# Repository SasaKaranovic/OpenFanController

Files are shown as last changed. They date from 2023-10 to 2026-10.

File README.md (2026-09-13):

# DIY OpenFAN Controller

## What is this project about?

DIY OpenFAN Controller (http://www.youtube.com/watch?v=C8tcsyASQRM "DIY OpenFAN Controller")

Above video shows the finished 10 channel PC fan controller, how it works and motivation behind some of the design decisions.

Some of the main features of the OpenFAN controller are:

- Individually control up to 10 fans
- USB communication with the host PC
- Has a built-in USB bootloader for smooth firmware upgrade experience
- GUI to control and monitor fans. Accessible locally/remotely through web browser
- Control fans by setting PWM percentage or target RPM
- Supports virtually unlimited number of custom fan profiles that you can create and apply through GUI/API
- Built in API interface for integration, (remote) monitoring or (remote) control.
- Built using simple off-the-shelf components to make it hacker/diy friendly
- Designed to be platform/OS agnostic and works on Windows, Linux and Mac
- GUI/API can be deployed as Docker application
- <a href="https://getfancontrol.com/" target="_blank">Fan Control</a> integration through <a href="https://github.com/SasaKaranovic/FanControl.OpenFan" target="_blank">FanControl.OpenFAN<a/> plugin (Windows)
- <a href="https://unraid.net/community/apps?q=OpenFanController#r" target="_blank">Unraid</a> docker integration through <a href="https://unraid.net/community/apps?q=OpenFanController#r" target="_blank">OpenFanController<a/> application (Unraid)
- <a href="https://github.com/SasaKaranovic/OpenFanController/pkgs/container/openfancontroller" target="_blank">Docker</a> image available (Docker)
<br/><br/>

## Can I buy OpenFAN controller

Yes you can. It's available on the [web shop](https://shop.sasakaranovic.com/products/openfan-pc-fan-controller).
<br/><br/>

## Can I build my own?

Yes you can. The above video explains the idea and how hardware and firmware works. It's recommended that you watch that first.

Hardware, Firmware and Software build instructions and source files are available in this repository.
<br/><br/>

## Is there documentation?

Documentation for OpenFAN Controller (and other projects) can be found at the official [docs page](https://docs.sasakaranovic.com/openfan/).
<br/><br/>

## What platforms are supported?

OpenFAN is designed to be platform agnostic. This means you can use it on Windows, Linux and Mac.

You can find more information on how to run OpenFAN software in the [software read me](Software)
<br><br>

Blog page: https://sasakaranovic.com/projects/openfan-controller/

YouTube video: http://www.youtube.com/watch?v=C8tcsyASQRM

<br/><br/>

#### Sasa Karanovic

<a href="https://sasakaranovic.com/" target="_blank" title="Sasa Karanovic Home Page"> Home Page</a> &nbsp;&middot;&nbsp;
<a href="https://youtube.com/c/sasakaranovic" target="_blank" title="Sasa Karanovic on YouTube"> YouTube</a> &nbsp;&middot;&nbsp;
<a href="https://github.com/sasakaranovic" target="_blank" title="Sasa Karanovic on GitHub"> GitHub</a> &nbsp;&middot;&nbsp;
<a href="https://twitter.com/_sasakaranovic_" target="_blank" title="Sasa Karanovic on Twitter"> Twitter</a> &nbsp;&middot;&nbsp;
<a href="https://instagram.com/_sasakaranovic_" target="_blank" title="Sasa Karanovic on Instagram"> Instagram</a> &nbsp;&middot;&nbsp;
<a href="https://github.com/sponsors/SasaKaranovic" target="_blank" title="Sponsor on GitHub"> Sponsor on GitHub</a>

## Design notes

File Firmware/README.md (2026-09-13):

# OpenFAN Controller - Firmware

## How to install latest firmware onto the board?

OpenFAN Controller supports loading new firmware over USB.

Latest firmware is compiled through GitHub action and published under [releases](https://github.com/SasaKaranovic/OpenFanController/releases). Download the latest firmware version to your PC.

To load the latest firmware onto your board, follow the below steps:

1. Disconnect all fans and power from the board
2. Hold the BOOT button
3. Connect USB-C cable to OpenFAN
4. You should see a new USB drive on your PC
5. Drag and drop (or copy-paste) the OpenFAN firmware
6. Within few seconds, the drive will disappear and you should see the white LED on the OpenFAN blinking
7. The board should be flashed and ready to go now
8. As a precaution and just to be 100% sure, you should power cycle the OpenFAN before using it.

## How to build firmware?

OpenFAN controller uses Pico2040 as the main microcontroller.

In order to build the firmware, you will need to install and setup Pico-SDK first. After that you can run `build.sh` script or manually run through the following steps

- `cmake -B {path-to-pico-sdk-directory} -S {path-to-OpenFAN-firmware-src-directory}`
- `cmake -C build`

If everything runs successfully, you should see a `build` folder and inside there should be a `.uf2` file that you can use for firmware upgrade.

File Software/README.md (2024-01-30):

# OpenFAN Controller - Software

## How to run the software?

There are many ways to run the OpenFAN software.

### Running from source [Win/Linux/Mac]

On any OS, if you have Python 3.9 (or higher) and PIP installed, you can run from source code.

1. Clone this repository and navigate to `Software/Python` folder.
2. Install Python dependencies by running `pip install -r requirements.txt`
3. Run the main application with `python webserver.py`
4. Open `http://localhost:3000` to access the Web GUI
<br><br>

### Running with Docker [Windows/Linux/Mac]

You can run OpenFAN in a Docker container.

Since with OpenFAN you can control fans remotely (via API and/or Web GUI), this can be very helpful for remotely managing fans on your servers or media stations.

To create a Docker container, log into your machine and run following commands

1. docker build github.com/sasakaranovic/openfancontroller -t sasakaranovic/openfan
2. docker run --name OpenFAN -p 3000:3000 --device=/dev/ttyACM0 -e OPENFANCOMPORT=/dev/ttyACM0 sasakaranovic/openfan:latest
3. Make sure you can access the server running this container and configure your firewall to allow port `3000` (if necessary)
4. Open `http://server-ip:3000` to access the Web GUI
<br><br>

### Using Fan Control [Windows]

You can use your OpenFAN directly from [Fan Control](https://getfancontrol.com/).

Fan Control is a highly focused fan controlling software for Windows.

To use OpenFAN with Fan Control, you can download the `FanControl.OpenFAN` plugin.

1. Install [Fan Control](https://getfancontrol.com/)
2. Download [FanControl.OpenFAN](https://github.com/SasaKaranovic/FanControl.OpenFan) plugin
3. Copy `FanControl.OpenFan.dll` to Fan Control's `Plugins` folder. (You might need to "unlock" the dll in its properties.)
4. Restart Fan Control
5. Fan Control will display all OpenFAN fan controls and RPM sensors
<br><br>

## How to debug/develop the software?

OpenFAN Controller is written in Python. In order to run the code, you will need to install Python 3.9 or higher.

After that, you will need to install the PIP Python package manager.

### Install dependencies

In order to install project dependencies you can open a terminal and navigate to the OpenFAN `Software/Python` directory.

Then type `pip install -r requirements.txt`

This will install all the necessary dependencies.

### How to run the server application

In your terminal, navigate to the `Software/Python` directory of OpenFAN and type `python webserver.py`

This will start the OpenFAN server. After this you can start using the gui through web browser by openning `https://localhost:3000` or use the API as described in the documentation.

### Running without Python or Docker?

There are multiple ways of converting a python code to an executable (ie. `py2exe`, `pyinstaller` etc).

There are many tutorials on how to do this depending on your operating system.

In the future, I will try to use GitHub Actions to generate binaries and installers that you can use to easily install and run OpenFAN software.

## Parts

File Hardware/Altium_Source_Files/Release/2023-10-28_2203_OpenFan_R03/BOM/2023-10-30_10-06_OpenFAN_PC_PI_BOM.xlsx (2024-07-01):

Designator | Manufacturer | Manufacturer Part Number | Quantity
C1 | KEMET | A768KE227M1DLAE029 | 1
C2, C4, C6, C10, C11, C12, C13, C14, C15, C16, C17, C18, C19, C21, C22, C24 | Samsung Electro-Mechanics | CL10B104KB8NNNC | 16
C5, C9, C20 | Samsung Electro-Mechanics | CL10A225KA8NNNC | 3
C7, C8 | Samsung Electro-Mechanics | CL10C070CB8NNNC | 2
C23_FCN1, C23_FCN2, C23_FCN3, C23_FCN4, C23_FCN5, C23_FCN6, C23_FCN7, C23_FCN8, C23_FCN9, C23_FCN10 | Samsung Electro-Mechanics | CL10A105KA8NNNC | 10
C25 | Samsung Electro-Mechanics | CL21A106KAYNNNE | 1
C26, C27 | Samsung Electro-Mechanics | CL21A226MAYNNNE | 2
D1 | ams-OSRAM USA INC. | LW Q38G-Q2OO-3K5L-1 | 1
F1, F2, F3 | Bel Fuse Inc. | 0ZCM0020FF2G | 3
L1 | Murata Electronics | LQM31PN4R7M00L | 1
P1 | Bestcreate Technology Limited | S150-M1A5T-003, S150-M2A5T-003, S150-M3A5T-003, | 1
P2 | Amphenol ICC (FCI) | 10118192-0001LF | 1
P4_FCN1, P4_FCN2, P4_FCN3, P4_FCN4, P4_FCN5, P4_FCN6, P4_FCN7, P4_FCN8, P4_FCN9, P4_FCN10 | Molex | 0470531000 | 10
R1, R2 | YAGEO | AC0603FR-0727RL | 2
R3 | YAGEO | RC0603FR-074K7L | 1
R4, R5, R11 | YAGEO | RC0603FR-0710KL | 3
R6, R15 | YAGEO | RC0603FR-071KL | 2
R7, R8, R10, R14, R16, R17 | YAGEO | RC0603FR-102K2L | 6
R9 | YAGEO | RC0603FR-10470RL | 1
R12 | YAGEO | RC0603FR-1015KL | 1
R13_FCN1, R13_FCN2, R13_FCN3, R13_FCN4, R13_FCN5, R13_FCN6, R13_FCN7, R13_FCN8, R13_FCN9, R13_FCN10 | YAGEO | RC0603FR-07100KL | 10
SW1, SW2 | E-Switch | TL1015AF160QG | 2
U1 | Winbond Electronics | W25Q32JVZPIQ | 1
U2 | Raspberry Pi | SC0914(13) | 1
U3, U4 | Microchip Technology | EMC2305-1-AP-TR | 2
U5 | Diodes Incorporated | AP63203WU-7 | 1
X1 | Abracon LLC | ABMM2-12.000MHZ-E2-T | 1

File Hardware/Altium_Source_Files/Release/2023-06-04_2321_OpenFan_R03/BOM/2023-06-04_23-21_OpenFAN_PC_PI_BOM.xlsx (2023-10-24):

Designator | Distributor | Distributor Part Number | Manufacturer | Manufacturer Part Number | Quantity
C1 | DigiKey | 399-A768KE227M1DLAE029TR-ND | KEMET | A768KE227M1DLAE029 | 1
C2, C4, C5, C6, C7, C8, C9, C10, C11, C12, C13, C14, C15, C16, C17, C18, C19, C20, C21, C22, C23_FCN1, C23_FCN2, C23_FCN3, C23_FCN4, C23_FCN5, C23_FCN6, C23_FCN7, C23_FCN8, C23_FCN9, C23_FCN10, C24, C25, C26, C27, D1, F1, F2, F3, L1, P1, P2, R1, R2, R3, R4, R5, R6, R7, R8, R9, R10, R11, R12, R13_FCN1, R13_FCN2, R13_FCN3, R13_FCN4, R13_FCN5, R13_FCN6, R13_FCN7, R13_FCN8, R13_FCN9, R13_FCN10, R14, R15, R16, R17, SW1, SW2 | [NoValue], DigiKey |  |  |  | 69
P3, P5 | DigiKey | A135088-ND | TE Connectivity AMP Connectors | 1546215-4 | 2
P4_FCN1, P4_FCN2, P4_FCN3, P4_FCN4, P4_FCN5, P4_FCN6, P4_FCN7, P4_FCN8, P4_FCN9, P4_FCN10 | DigiKey | WM4330-ND | Molex | 0470531000 | 10
U1 | DigiKey | W25Q32JVZPIQ-ND | Winbond Electronics | W25Q32JVZPIQ | 1
U2 | DigiKey | 2648-SC0914(13)CT-ND | Raspberry Pi | SC0914(13) | 1
U3, U4 | DigiKey | EMC2305-1-AP-CT-ND | Microchip Technology | EMC2305-1-AP-TR | 2
U5 | DigiKey | AP63203WU-7DICT-ND | Diodes Incorporated | AP63203WU-7 | 1
X1 | DigiKey | 535-9631-1-ND | Abracon LLC | ABMM2-12.000MHZ-E2-T | 1

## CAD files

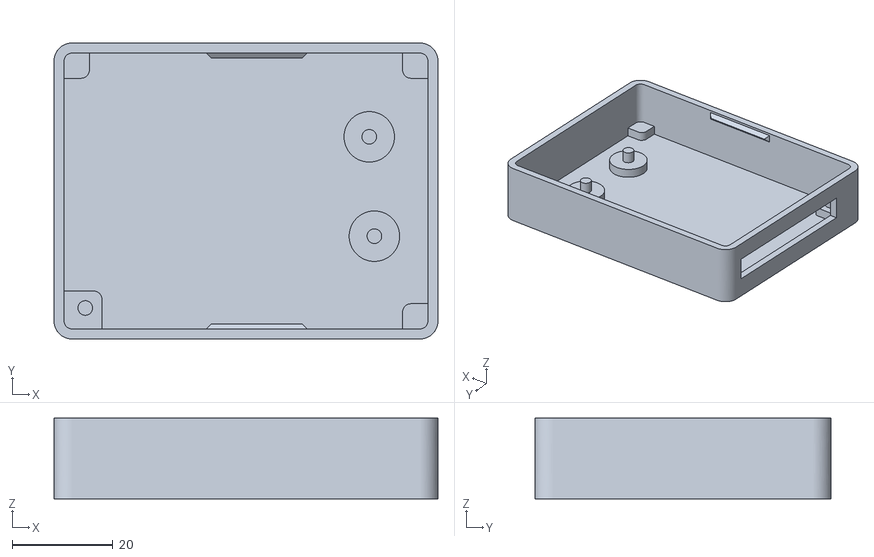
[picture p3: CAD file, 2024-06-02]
Enclosure/Rev1/Enclosure_OpenFAN_Bottom.stl
76.1 x 58.7 x 16.0

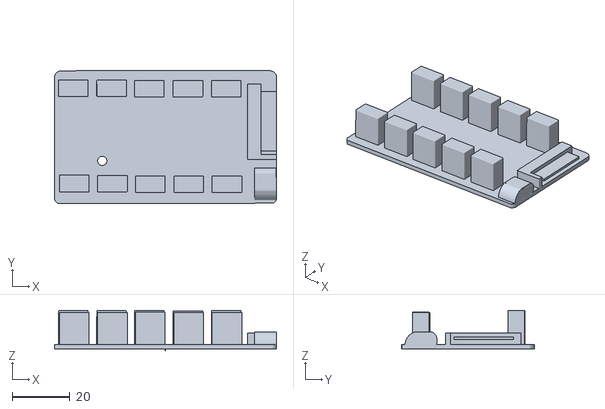
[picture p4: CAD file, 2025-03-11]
Enclosure/Rev2_by_Joe_Dutson/New_V7_PCB.stl
77.0 x 46.0 x 13.9

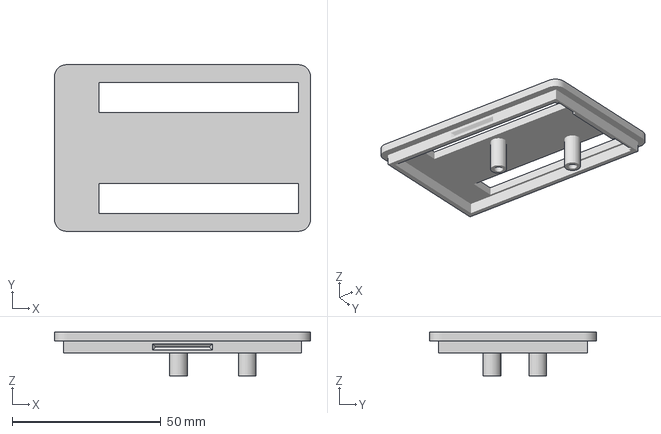
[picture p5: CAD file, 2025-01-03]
Enclosure/Rev2_by_Sam_Chan/Top-PCB-Enclosure_by_Sam_Chan.3mf
86.0 x 56.0 x 14.7 mm

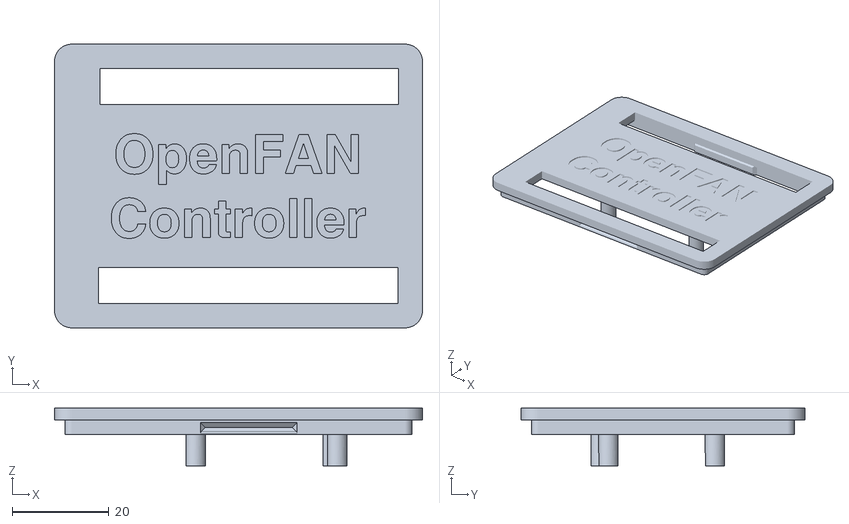
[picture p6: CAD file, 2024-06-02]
Enclosure/Rev1/Enclosure_OpenFAN_Top.stl
76.1 x 58.7 x 11.9

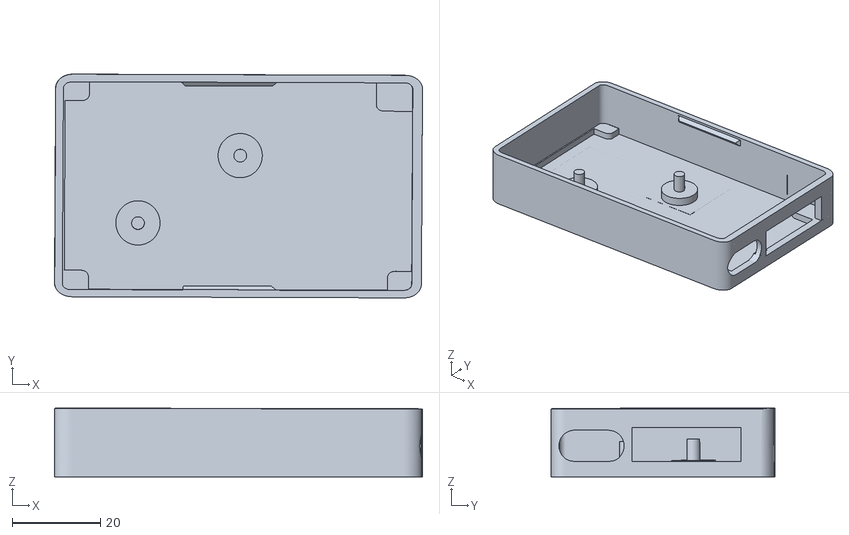
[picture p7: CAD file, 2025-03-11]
Enclosure/Rev2_by_Joe_Dutson/New_V7_Bottom.stl
83.2 x 50.6 x 15.6

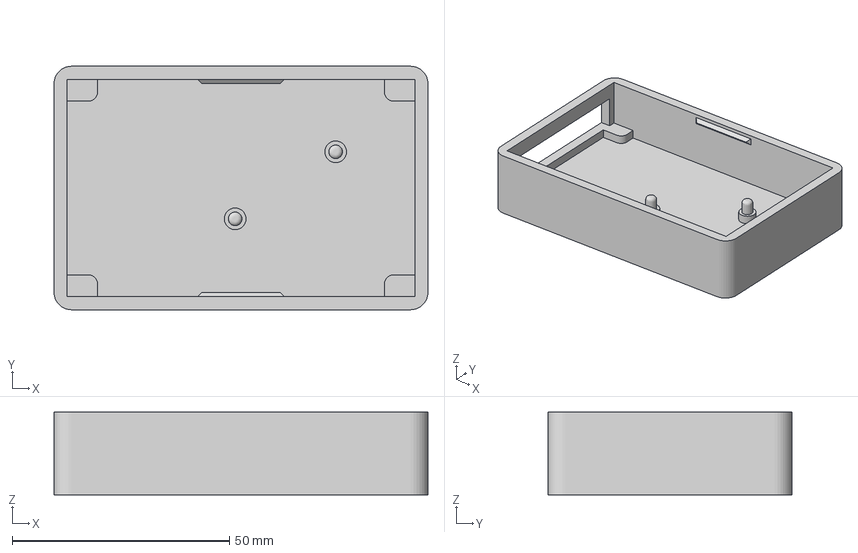
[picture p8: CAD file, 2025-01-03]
Enclosure/Rev2_by_Sam_Chan/Bottom-PCB-Enclosure_by_Sam_Chan.3mf
86.0 x 56.0 x 19.0 mm

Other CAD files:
Enclosure/Rev1/Fusion360_OpenFAN_Enclosure.f3z

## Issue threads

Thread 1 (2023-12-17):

Temperature sensors

Miggas, 2023-12-17:
Would it be possible to implement the ability to use temperature sensors?, I'm currently using 2, and this would be useful to make a Fan/Pump curve to the water temperature instead of the CPU/GPU temps.
I'm also planning on sharing the design, as I'm building a Big Corsair Fan HUB to control both Fan speeds and their RGB using https://github.com/Legion2/CorsairLightingProtocol

Miggas, 2023-12-17:
Also would it be possible to implement the ability to use temperature sensors?, I'm currently using 2, and this would be useful to make a Fan/Pump curve to the water temperature instead of the CPU/GPU temps

SasaKaranovic, 2024-01-28:
Hey @Miggas

Yes it would be fairly easy to add support for one or more temperature sensors.
Are you using them with OpenFAN board? How many sensors do you have and what type/pn?

Miggas, 2024-01-28:
Temperature probe type: NTC, 10KΩ at 25°C
They are the most common type of temp probe used in water cooling loops.

SasaKaranovic, 2024-01-29:
Currently OpenFAN does not support analogue sensors, only digital ones (I2C or 1-Wire).
But maybe in the next revision we can add support for analogue/NTC sensors.

lietu, 2024-12-04:
Why is this closed? I don't see any support for NTC thermal probes which are incredibly standard in the PC world.

laleeroy, 2025-03-14:
Any updates to this? Would love to see this

Closed 2024-01-29.

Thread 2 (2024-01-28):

Plugin for Fan Control

SasaKaranovic, 2024-01-28:
[Fan Control](https://getfancontrol.com/) is very popular fan control software for Windows.

Fan Control [plugin system](https://github.com/Rem0o/FanControl.Releases/wiki/Plugins) allows adding additional sensors and controls which would allow us to integrate OpenFAN natively and/or through the API.

SasaKaranovic, 2024-01-29:
Created initial version of the plugin [FanControl.OpenFAN](https://github.com/SasaKaranovic/FanControl.OpenFan)

SasaKaranovic, 2024-01-30:
OpenFAN plugin for Fan Control released.

Closed 2024-01-30.

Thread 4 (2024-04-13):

USB CDC serial stops working

MRezaNasirloo, 2024-04-13:
I don't have the board, but I installed the firmware on an RP2040 board to confirm a bug that I had with the TinyUSB library. When the host Windows PC wakes up from sleep, the USB CDC does not respond anymore. It only starts functioning after a USB replug or restart. This might be related to this issue: https://github.com/hathach/tinyusb/issues/1416.

Could you confirm if you have been able to reproduce this issue?

Thank you.

SasaKaranovic, 2024-04-13:
Hi @MRezaNasirloo!
I have not been able to reproduce this and I believe it should not affect OpenFAN since it is SATA powered, not USB powered.

Closed 2024-04-13.

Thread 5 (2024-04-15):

No monitor and not command issues

PaoloGB, 2024-04-15:
Hi Sasa,
first of all, thank you for sharing this project. It is a fan gadget to have.

I manufactured my PCB, flashed it with the FW and can get to the point where I have the server running and the webpage displayed.
However, I get not readback from the fans

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

Looking at the server output, it seems to hang after the first command. Pressing any button on the page does not produce any further output in the terminal.
Normally I would think this is due to the I2C bus hanging, but looking at the lines on a scope, I can see activity and, as far as I can tell, even ACK from the drivers.

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

I have tried several browsers, in case it was a websocket issue, but still got no luck.
Any chance you have seen this before and could point me in the right direction to get the device to work?

`←[0;36mApr 15 2024 11:26:48.688←[0m ←[1;31mpid:30136←[0m ←[0;34mbase_logger.py            62←[0m ←[1;33mINFO ←[0m ←[0;32mLogging level: DEBUG←[0m
←[0;36mApr 15 2024 11:26:48.695←[0m ←[1;31mpid:30136←[0m ←[0;34mconfig.py                 46←[0m ←[1;33mDEBUG←[0m ←[0;32mServer config:←[0m
←[0;36mApr 15 2024 11:26:48.695←[0m ←[1;31mpid:30136←[0m ←[0;34mconfig.py                 55←[0m ←[1;33mDEBUG←[0m ←[0;32m{'hostname': 'localhost', 'port': 3000, 'communication_timeout
': 1}←[0m
←[0;36mApr 15 2024 11:26:48.695←[0m ←[1;31mpid:30136←[0m ←[0;34mconfig.py                 57←[0m ←[1;33mDEBUG←[0m ←[0;32mHardware config:←[0m
←[0;36mApr 15 2024 11:26:48.695←[0m ←[1;31mpid:30136←[0m ←[0;34mconfig.py                 66←[0m ←[1;33mDEBUG←[0m ←[0;32m{'port': None}←[0m
←[0;36mApr 15 2024 11:26:48.695←[0m ←[1;31mpid:30136←[0m ←[0;34mconfig.py                 68←[0m ←[1;33mDEBUG←[0m ←[0;32mFan profile config:←[0m
←[0;36mApr 15 2024 11:26:48.695←[0m ←[1;31mpid:30136←[0m ←[0;34mconfig.py                 77←[0m ←[1;33mDEBUG←[0m ←[0;32m{'1000 RPM': {'type': 'rpm', 'values': [1000, 1000, 1000, 1000
, 1000, 1000, 1000, 1000, 1000, 1000], 'name': '1000 RPM'}, 'MadMax': {'type': 'PWM', 'values': [100, 100, 100, 100, 100, 100, 100, 100, 100, 100]}, '1200RPM': {'type': 'RPM', 'values
': [1200, 1200, 1200, 1200, 1200, 1200, 1200, 1200, 1200, 1200]}}←[0m
←[0;36mApr 15 2024 11:26:48.707←[0m ←[1;31mpid:30136←[0m ←[0;34mFanCommander.py          104←[0m ←[1;33mDEBUG←[0m ←[0;32mSearching for COM port with VID:0x2E8A and PID:0x000A←[0m
←[0;36mApr 15 2024 11:26:48.707←[0m ←[1;31mpid:30136←[0m ←[0;34mFanCommander.py          106←[0m ←[1;33mDEBUG←[0m ←[0;32mCOM10←[0m
←[0;36mApr 15 2024 11:26:48.707←[0m ←[1;31mpid:30136←[0m ←[0;34mFanCommander.py          107←[0m ←[1;33mDEBUG←[0m ←[0;32m       Product: None←[0m
←[0;36mApr 15 2024 11:26:48.707←[0m ←[1;31mpid:30136←[0m ←[0;34mFanCommander.py          108←[0m ←[1;33mDEBUG←[0m ←[0;32m       Desc: USB Serial Device (COM10)←[0m
←[0;36mApr 15 2024 11:26:48.708←[0m ←[1;31mpid:30136←[0m ←[0;34mFanCommander.py          109←[0m ←[1;33mDEBUG←[0m ←[0;32m       SN: DE615063CF7F2939←[0m
←[0;36mApr 15 2024 11:26:48.708←[0m ←[1;31mpid:30136←[0m ←[0;34mFanCommander.py          110←[0m ←[1;33mDEBUG←[0m ←[0;32m       VID:11914 PID:10←[0m
←[0;36mApr 15 2024 11:26:48.708←[0m ←[1;31mpid:30136←[0m ←[0;34mFanCommander.py          111←[0m ←[1;33mDEBUG←[0m ←[0;32m       Location: 1-8:x.2←[0m
←[0;36mApr 15 2024 11:26:48.708←[0m ←[1;31mpid:30136←[0m ←[0;34mFanCommander.py          112←[0m ←[1;33mDEBUG←[0m ←[0;32m       Interface: None←[0m
←[0;36mApr 15 2024 11:26:48.708←[0m ←[1;31mpid:30136←[0m ←[0;34mFanCommander.py          114←[0m ←[1;33mDEBUG←[0m ←[0;32mUsing 'USB Serial Device (COM10)' as Fan Controller COM port←[
0m
←[0;36mApr 15 2024 11:26:48.708←[0m ←[1;31mpid:30136←[0m ←[0;34mwebserver.py             231←[0m ←[1;33mINFO ←[0m ←[0;32mUsing COM port `COM10 - USB Serial Device (COM10)` (Found thro
ugh USB VID:PID).←[0m
←[0;36mApr 15 2024 11:26:48.708←[0m ←[1;31mpid:30136←[0m ←[0;34mwebserver.py             233←[0m ←[1;33mINFO ←[0m ←[0;32mFan Controller port: COM10 - USB Serial Device (COM10)←[0m
←[0;36mApr 15 2024 11:26:48.713←[0m ←[1;31mpid:30136←[0m ←[0;34mserial_driver.py          43←[0m ←[1;33mDEBUG←[0m ←[0;32mSerial driver initialized with←[0m
←[0;36mApr 15 2024 11:26:48.713←[0m ←[1;31mpid:30136←[0m ←[0;34mserial_driver.py          44←[0m ←[1;33mDEBUG←[0m ←[0;32m-- flush_on_write: 'True'←[0m
←[0;36mApr 15 2024 11:26:48.713←[0m ←[1;31mpid:30136←[0m ←[0;34mserial_driver.py          45←[0m ←[1;33mDEBUG←[0m ←[0;32m-- timeout: '2'←[0m
←[0;36mApr 15 2024 11:26:48.713←[0m ←[1;31mpid:30136←[0m ←[0;34mwebserver.py             258←[0m ←[1;33mINFO ←[0m ←[0;32mKaranovic Research OpenFan - Starting API server←[0m
←[0;36mApr 15 2024 11:26:48.714←[0m ←[1;31mpid:30136←[0m ←[0;34mwebserver.py             263←[0m ←[1;33mINFO ←[0m ←[0;32mListening on port 3000←[0m
←[0;36mApr 15 2024 11:26:48.873←[0m ←[1;31mpid:30136←[0m ←[0;34mwebserver.py             129←[0m ←[1;33mINFO ←[0m ←[0;32mRequest:STATUS--------------←[0m
←[0;36mApr 15 2024 11:26:48.873←[0m ←[1;31mpid:30136←[0m ←[0;34mFanCommander.py           50←[0m ←[1;33mDEBUG←[0m ←[0;32m===DEBUG1======←[0m
←[0;36mApr 15 2024 11:26:48.875←[0m ←[1;31mpid:30136←[0m ←[0;34mFanCommander.py           52←[0m ←[1;33mDEBUG←[0m ←[0;32m===DEBUG2======←[0m
←[0;36mApr 15 2024 11:26:48.875←[0m ←[1;31mpid:30136←[0m ←[0;34mFanCommander.py           59←[0m ←[1;33mDEBUG←[0m ←[0;32m===DEBUG4======←[0m
←[0;36mApr 15 2024 11:26:48.875←[0m ←[1;31mpid:30136←[0m ←[0;34mFanCommander.py           24←[0m ←[1;33mDEBUG←[0m ←[0;32mCMD:0 Data: None←[0m
←[0;36mApr 15 2024 11:26:48.875←[0m ←[1;31mpid:30136←[0m ←[0;34mFanCommander.py           25←[0m ←[1;33mDEBUG←[0m ←[0;32mSending `>00`←[0m
`

PaoloGB, 2024-04-15:
[new 1.txt](https://github.com/SasaKaranovic/OpenFanController/files/14977686/new.1.txt)

Uploading the terminal output again

PaoloGB, 2024-04-15:
Looking at the uart, I see a bunch of these
```
[0001096429][E][EMC230X] emc230x_send_then_read: write error 0x01
[0001096429][E][EMC230X] emc230x_send_then_read: write error 0x01
[0001096429][E][EMC230X] emc230x_send_then_read: read error 0x01
```
which would seem to indicate the I2C transaction timed out. However at the moment I am stuck, as I can't compile the FW without the logger source file so I can't try to write debug code into it.

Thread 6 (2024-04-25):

Switch from Altium to Kicad

EinRainerZufall, 2024-04-25:
I think it would be better for an open source project to use Kicad so that more people can edit and improve the PCB.

I have already started and created the schematic.

SasaKaranovic, 2024-04-26:
Hi @EinRainerZufall
Thanks for the suggestion.
Altium has a free tier that is available and can be used online.
I personally do not use Kicad so that would not work for me.

Closed 2024-04-26.

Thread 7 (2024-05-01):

Itemised BOM list & Thermal Fuse Values?

azzajess, 2024-05-01:
Hey

I have been trying to figure out the components for a bom list for PCB assembly from pcbway, and realised there are quite a number of components that dont have have values listed in the BOM, so I have been slowly filling it out.

What Im mainly asking however, is what are the values of the Thermal Fuses/PTC fuses? There doesn't look to be any information that I can gather from the files provided.
This is my BOM list so far. Only thing missing is the thermal fuses and the sata connector.

Thanks in advance for the information

Update: Found the sata connector from someone on ali that doesn't require 1000moq.
Update 2: Rearanged to match PCBWay BOM and fixed a wrong resistor value
update 3: I figured out the fuses are for output draw (assuming sensors) so I just put a lowish current value fuse since they generally dont consume much current. I also fixed some capacitor voltage ratings there were wrong...Sent this version to PCBway. See what happens
Update 4: Removed the block terminals as I got the wrong size in the BOM list and its really not required tbh. Also PCBWAY Cant order from Aliexpress for us, so I had to order it separately and solder it myself.

[2023-06-04_23-21_OpenFAN_PC_PI_BOM.Updated.4.xlsx](https://github.com/SasaKaranovic/OpenFanController/files/15445882/2023-06-04_23-21_OpenFAN_PC_PI_BOM.Updated.4.xlsx)

Closed 2024-06-16.

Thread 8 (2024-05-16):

API documentation typo

EinRainerZufall, 2024-05-16:
I noticed that when setting the RPM the fan index is based on 0.

The first fan:
`http://192.168.0.11:3210/api/v0/fan/0/rpm?value=1000`

The tenth fan:
`http://192.168.0.11:3210/api/v0/fan/9/rpm?value=1000`

And if you select 10, the following error occurs:
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

&nbsp;
&nbsp;

And when setting the PWM, the same error occurs:
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

EinRainerZufall, 2024-05-16:
The first error may be intentional and only the docu is wrong? Because the docu says that the index is `1-10`.

SasaKaranovic, 2024-05-17:
Hey @EinRainerZufall !

Thank you for catching this! You are absolutely right. There is a typo in the documentation.
The fan indexing should range from 0-9 instead of 1-10... I will fix that now.

https://github.com/SasaKaranovic/OpenFanController/blob/master/Software/Python/webserver.py#L242,L244

EinRainerZufall, 2024-05-17:
Hi @SasaKaranovic

I continued testing today and found the error for setting a PWM value in the code.

According to the docu:
`http://192.168.0.11:3210/api/v0/fan/6/pwm?value=100`

but it is actually programmed:
`http://192.168.0.11:3210/api/v0/fan/6/set?value=100`

&nbsp;
&nbsp;
I think `pwm` would be better for clarity, but that would be a breaking change

SasaKaranovic, 2024-05-18:
Hey @EinRainerZufall !

Thank you for bringing this up. Another typo in the documentation that should be fixed now.

And I agree, `pwm` would make more sense for clarity but I am also reluctant to introduce breaking changes now...
Maybe I can add support for both `pwm` and `set` and then "phase out" `set` over time.

Closed 2024-05-17.

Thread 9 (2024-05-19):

Stop Fans possible?

Fabian-Schmidt, 2024-05-19:
Do I see it correctly that you always supply 12V to the fan?

Some Fan understand 0% PWM signal as a stop and others spin at minimal speed.
Without means of interrupting power to the fan it is not possible to guarantee to stop a fan for a silent mode.

SasaKaranovic, 2024-05-19:
Hey Fabian.

OpenFAN controls the fans via PWM signal.

So at 0% PWM the fan will be at whatever state the fan manufacturer designed as minimum speed. Which should be OFF but there are fan manufacturers that deviate from this.

LoLo2207, 2025-01-14:
Sorry for reviving this, could it be possible to add in a V4 some kind of relays or transistors to turn off each channel? Because there are fans that don't have the 0RPM mode

SasaKaranovic, 2025-01-18:
Hey @LoLo2207

Thank you for the suggestion. I can't promise anything other than it's already on the feature "wish-list" for next iteration.

Just briefly explaining some reasoning why this is not already a feature;
Adding such feature is very simple but it does increase overall complexity and cost. And the latter would be passed on to everyone regardless if they really need that feature or "don't care" about it.

SasaKaranovic, 2025-01-18:
For anyone reading this issue in the future and wondering why 0% PWM makes some fans stop and some are still spinning, here is the original [Intel 4-pin PWM specification](https://www.konilabs.net/docs/standards/fan/intel_4wire_pwm_fans_specs_rev1_2.pdf).

On `page 12`, `Figure 2 Fan Speed Response to PWM Control Input Signal` it shows that PWM below 20% is lebeled as "undetermined".
This usually leaves fan manufacturer to choose between having their fan stop completely (0 RPM) below certain PWM or have them run at some minimum (non-zero) RPM.

Closed 2024-06-01.

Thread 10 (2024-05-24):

Bug in website

EinRainerZufall, 2024-05-24:
First of all, sorry for all the issues I opened^^

If you switch to PWM mode on the website and then go back to RPM mode, the speed is locked to `OFF`

I'm not that good at programming websites, but in my opinion the mistake is that you query the label as a number and then set it to `OFF` with this IF query without being able to reset it.

https://github.com/SasaKaranovic/OpenFanController/blob/master/Software/Python/webpage/assets/js/kr_gui_fan_status.js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,L353

SasaKaranovic, 2024-05-25:
First of all, no apology needed. You are taking your time to improve this project and help everyone else and I really appreciate that! :)

Seems like you have a reliable way of reproducing this issue. Which is always very helpful and key to fixing them.
Do you mind providing step-by-step actions to reproduce this issue?
Also feel free to add notes for relevant steps, like for example what is the expected behavior vs what is observed behavior.

EinRainerZufall, 2024-05-25:
The steps are basically as described above:

1. switch to PWM mode on the main page
2. then switch back to RPM mode

Then you will only see "OFF" as the RPM target and you have to reload the website to set a speed

And I would expect that if you move the sliders that the speed changes from "OFF" to a real speed

SasaKaranovic, 2024-05-25:
I don't know how I missed that typo... thank you for mentioning it!
It should be fixed not.

EinRainerZufall, 2024-05-25:
ok I have updated my Docker, but the error is still there

SasaKaranovic, 2024-05-25:
Make sure to clear your cache (ie CTRL+F5) or use a different browser to make sure you are not looking at a cached version.

EinRainerZufall, 2024-05-25:
The website was still in cache, everything works as it should. Thanks for the fix.

Closed 2024-05-26.

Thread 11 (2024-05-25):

Live preview feature

SasaKaranovic, 2024-05-25:
When creating a fan profile, there could be an option for "live preview" (ie check box).
This feature would apply the rpm/pwm values that are assigned to each fan in real-time.
Such option would be helpful when creating custom profiles so end-user can in real-time see what is the amount of noise/air-flow for each fan.

Closed 2024-06-16.

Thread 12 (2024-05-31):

Fan alias feature

Th3M1k3y, 2024-05-31:
It would be nice to have the ability to rename fans in the UI.

Maybe something like Alias <sub>(FAN #1)</sub>

Control through the API remain as it is currently.

SasaKaranovic, 2024-06-01:
Thanks for the suggestion! I like this idea.

lord-xeon, 2024-06-02:
I also would like this feature.  I started to build something to keep track of the same for me.  While it's probably not a problem for everyone, it's nice to know `Fan 6` is the one on the top of the case.

SasaKaranovic, 2024-06-02:
@Th3M1k3y @lord-xeon

I have just created a new branch https://github.com/SasaKaranovic/OpenFanController/tree/sk_general_improvements that contains API paths that allow setting of fan alias (name).

The UI is also updated to show aliases (if set).
To set an alias, you would double-click on the fan name and the pop-up will appear asking for new fan name.

If you have the chance, please give it a try and let me know if you have any suggestions.
I will take couple of days to test and make sure there are no issues or regressions and then if everything looks alright merge it into master.

Th3M1k3y, 2024-06-02:
I am running the controller in the unraid docker, not sure how to go about testing this.

SasaKaranovic, 2024-06-02:
>  I am running the controller in the unraid docker, not sure how to go about testing this.

You would have to run it manually or build a new docker image.
It's ok if it's not convenient for you, I will release a new docker image once it's tested and then you can just update your container.

SasaKaranovic, 2024-06-21:
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

This feature should be live now in the release branch.
If you update (force-update) your docker image, you should have this option.
Double-click on the fan name will show a prompt to enter a new fan name.

Let me know how it works and if you encounter any issues.

Closed 2024-07-28.

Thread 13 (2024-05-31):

Fan group

Th3M1k3y, 2024-05-31:
Being able to put fans into groups could be useful.

When a fan group is added, the group is added to the list of fans, and the fans in the group is hidden from the dropdown.
Selecting the group and manually applying a fan setting would then set all the fans in the group to the selected manual setting.

Controlling fans through the API could be done something like

`/api/v0/fan/{group}/rpm?value={rpm}`

SasaKaranovic, 2024-06-01:
Hey there! Thanks for the suggestion!

What would be the benefit of using fan groups instead of creating fan profiles?
Or maybe you have a very specific use-case in mind that this feature would be helpful for and can't use profiles for it?

In my use-cases, either the fans are being controlled automatically by a third party app (ie FanControl on Windows) or each individual fan is controlled programmatically (through scripting/automation or on Unraid via [OpenFAN Unraid Service](https://github.com/SasaKaranovic/OpenFanUnraidService))

Also consider that adding groups feature to the API would potentially make things very opaque.
Consider the example you suggested `/api/v0/fan/{group}/rpm?value={rpm}`.
It is not immediately obvious which fans are going to be set to this RPM value.
Can a single fan be a part of two groups? If yes, what happens if there is a conflict (both groups get request for different RPM).
Or if you remove a fan from a group, how doe the application on the other end (ie third party app) get notified of this and how should it handle this?

Honestly... I like and dislike this idea at the same time.
Maybe because I don't fully understand how this would work or maybe because I'm a bit worried about introducing "unnecessary" complexity or confusing end-users.

But I would love to hear more on this.
So please whenever you get a chance share your thoughts and other people please feel free to chime in if you have anything to add.

Th3M1k3y, 2024-06-01:
> Hey there! Thanks for the suggestion!
>
> What would be the benefit of using fan groups instead of creating fan profiles? Or maybe you have a very specific use-case in mind that this feature would be helpful for and can't use profiles for it?

The group of fans would not replace the profiles, it would just group some or all fans together so all are controlled at the same time.

> Also consider that adding groups feature to the API would potentially make things very opaque. Consider the example you suggested `/api/v0/fan/{group}/rpm?value={rpm}`. It is not immediately obvious which fans are going to be set to this RPM value. Can a single fan be a part of two groups? If yes, what happens if there is a conflict (both groups get request for different RPM). Or if you remove a fan from a group, how doe the application on the other end (ie third party app) get notified of this and how should it handle this?

Fans would only be able to be in one group, which is why fans in a group is removed from the dropdown list.

My idea was based on the case I got, where I got 3 fans in the front. Instead of making 3 calls to set the fan speeds, it could be set by just setting the group instead.

I didn't consider how an third party app would/should handle it. Showing which fan's was set could be an array in the returned JSON, and then leave it up to the app creator to decide if they want to handle changes.

> Honestly... I like and dislike this idea at the same time. Maybe because I don't fully understand how this would work or maybe because I'm a bit worried about introducing "unnecessary" complexity or confusing end-users.

Maybe this isn't the best approach either, but maybe it can plant a seed for a better idea. :)

The thinking behind my idea, was like instead of connecting the fan's together with a cable, it could be done virtually and that way keep the individual rpm monitoring.

SasaKaranovic, 2024-06-02:
> The group of fans would not replace the profiles, it would just group some or all fans together so all are controlled at the same time.

> My idea was based on the case I got, where I got 3 fans in the front. Instead of making 3 calls to set the fan speeds, it could be set by just setting the group instead.

Maybe a better and less convoluted solution would be to add another API path that allows you to set multiple fans at once?
Something like `/api/v0/fan/multiple/set?value=0:1200;1:1000;2:1500`.
This call would then result in `Fan 0 -> 1200 RPM`, `Fan 1 -> 1000 RPM` and `Fan 2 -> 1500 RPM`.

> I didn't consider how an third party app would/should handle it. Showing which fan's was set could be an array in the returned JSON, and then leave it up to the app creator to decide if they want to handle changes.

I would like to avoid putting any additional burden on the external application(s).
Especially since in some cases they can be very simple scripts that just make the API based on some event.
For this reason it might make more sense (and it's probably less convoluted and more transparent) to keep this grouping information in the external application.
Mainly because if the external application already knows that there is a need to control fans 0, 3, 5 as single unit, making multiple API calls (or one if the above API change is implemented) makes more sense than making changes in two places (one in the OpenFAN to configure groups and then another in the external app to control those groups).

Out of curiosity how are you using your OpenFAN and how are you automating your fan control?
I am assuming you don't change fan speed multiple times a second (which you _really_ should not be doing anyway), so making multiple API calls vs single API call for fan group should have barely any performance or resource benefit.

Th3M1k3y, 2024-06-02:
> Maybe a better and less convoluted solution would be to add another API path that allows you to set multiple fans at once? Something like `/api/v0/fan/multiple/set?value=0:1200;1:1000;2:1500`. This call would then result in `Fan 0 -> 1200 RPM`, `Fan 1 -> 1000 RPM` and `Fan 2 -> 1500 RPM`.

That would work too

> Out of curiosity how are you using your OpenFAN and how are you automating your fan control? I am assuming you don't change fan speed multiple times a second (which you _really_ should not be doing anyway), so making multiple API calls vs single API call for fan group should have barely any performance or resource benefit.

Right now I am using https://github.com/SasaKaranovic/OpenFanUnraidService in my server, but I am also going to make something of my own at some point. I am not concerned about performance, I just like the workflow where I build up what needs to happen, then send it all over in one go.

SasaKaranovic, 2024-06-17:
I've added it on the to-do list but it's very low priority because you can get same result by making multiple requests.
Obviously we can argue that making one request is more "elegant" but these requests should not be made manually anyway.

Closed 2024-07-08.

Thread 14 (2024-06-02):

Make better use of HTTP methods

lord-xeon, 2024-06-02:
I'm trying to build a UI around this service and the HTTP server doesn't follow some best practices.

1. Setting fan values is a `GET` that makes changes to something, that should be a `PUT`
2. Making a new profile is a POST, but it uses query string params, ideally, that should be the `payload` of the POST
3. Removing profiles should be a `DELETE` or a `PUT`

SasaKaranovic, 2024-06-02:
Hey @lord-xeon thanks for the suggestion and taking the time to post it.
Also I would love if you share that UI when it's available. :)

If this was a REST API for purely service-to-service interaction or some other web only interface I would agree.
But in this case I don't necessarily agree that mainly using `GET` is wrong or a bad practice.
Especially if you consider that we want to allow virtually anything to interact with the OpenFAN API.
So if for whatever reason the third-party script/app is unable (or requires some extra work) to send `PUT` request instead of `GET`, it would raise the entry bar for interacting with the API and potentially prevent some users from using it or cause unnecessary "pain points".

But with that said, if using more explicit HTTP methods (ie `PUT`, `DELETE` etc) makes anyone's life easier or removes any road-blocks for future development, we could alias them so both are valid and accepted by the API.

Closed 2024-06-23.

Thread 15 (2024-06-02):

Update enclosure height to fit latest batch of board

Th3M1k3y, 2024-06-02:
A capacitor is too tall, so the lid can't be closed.

I added a hole so the capacitor could go through. With this the surface of the capacitor sits 0.1mm under the surface of the lid.

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

SasaKaranovic, 2024-06-02:
Thank you @Th3M1k3y !

I have been informed that the PCB shop used a slightly taller capacitor in this batch.
As the result it is colliding with the enclosure.
I will update the enclosure design to make it taller so it fits the board nicely.

SasaKaranovic, 2024-06-02:
@Th3M1k3y
I have just updated the enclosure by increasing the height by 2mm.
If you want you can print the new enclosure and give it a try.
If it works well for you too, let me know and we can close this issue.

Closed 2024-06-17.

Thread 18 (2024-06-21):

Self made board: Not working with Fan Control software

RysatkoCZ, 2024-06-21:
Hello.
First, thank you for this awesome project.
I wanted to increase fan ports in my mITX system so I built OpenFan Controller. I am using Fan Control to control fans in my system. But after connecting the controller to the motherboard the Fan Control stops updating the sensors until I disconnect the controller. When I try to restart the Fan Control it will not open until the controller is disconnected or the plugin .dll removed from the Plugins folder. I am using Fan Control V194, FanControl.OpenFAN plugin v20240129 and OpenFan firmware 2023-09-29_OpenFAN_FW_01.uf2.

SasaKaranovic, 2024-06-22:
Hey @RysatkoCZ !

I assume this is a custom built boards?
Did you assemble it yourself or did you have a PCB shop do it for you?

OpenFAN works with FanControl. I have it running on my PC (just updated to v194 from v193) and have multiple other people report that they are using it with FanControl using the provided plugin.

This means that most likely there is an issue with your board.

Have you double checked your hardware?
For example the white LED should be blinking when unit is programmed.
You can manually send commands over serial to check if your board is receiving commands properly and checking response.
You can run the provided python software and check the logs if there are any errors/issues reported.

RysatkoCZ, 2024-06-23:
The board was assembled by PCBway. The LED is blinking slowly after firmware flashing.
I am trying to run the python software but still get error when building it.

```
PS C:\Users\Pavel\Downloads\OpenFanController-master\Software\Python> pip install -r requirements.txt
Collecting tornado>=6.3.3 (from -r requirements.txt (line 1))
  Using cached tornado-6.4.1-cp38-abi3-win_amd64.whl.metadata (2.6 kB)
Collecting argparse (from -r requirements.txt (line 2))
  Using cached argparse-1.4.0-py2.py3-none-any.whl.metadata (2.8 kB)
Collecting pyserial==3.5 (from -r requirements.txt (line 3))
  Using cached pyserial-3.5-py2.py3-none-any.whl.metadata (1.6 kB)
Collecting ruamel.yaml==0.17.21 (from -r requirements.txt (line 4))
  Using cached ruamel.yaml-0.17.21-py3-none-any.whl.metadata (13 kB)
Collecting ruamel.yaml.clib==0.2.7 (from -r requirements.txt (line 5))
  Using cached ruamel.yaml.clib-0.2.7.tar.gz (182 kB)
  Installing build dependencies ... done
  Getting requirements to build wheel ... done
  Preparing metadata (pyproject.toml) ... done
Using cached pyserial-3.5-py2.py3-none-any.whl (90 kB)
Using cached ruamel.yaml-0.17.21-py3-none-any.whl (109 kB)
Using cached tornado-6.4.1-cp38-abi3-win_amd64.whl (438 kB)
Using cached argparse-1.4.0-py2.py3-none-any.whl (23 kB)
Building wheels for collected packages: ruamel.yaml.clib
  Building wheel for ruamel.yaml.clib (pyproject.toml) ... error
  error: subprocess-exited-with-error

  × Building wheel for ruamel.yaml.clib (pyproject.toml) did not run successfully.
  │ exit code: 1
  ╰─> [119 lines of output]
      <string>:81: DeprecationWarning: ast.Str is deprecated and will be removed in Python 3.14; use ast.Constant instead
      <string>:81: DeprecationWarning: ast.Num is deprecated and will be removed in Python 3.14; use ast.Constant instead
      <string>:81: DeprecationWarning: ast.Bytes is deprecated and will be removed in Python 3.14; use ast.Constant instead
      <string>:81: DeprecationWarning: ast.NameConstant is deprecated and will be removed in Python 3.14; use ast.Constant instead
      <string>:103: DeprecationWarning: ast.Str is deprecated and will be removed in Python 3.14; use ast.Constant instead
      <string>:107: DeprecationWarning: ast.Bytes is deprecated and will be removed in Python 3.14; use ast.Constant instead
      <string>:109: DeprecationWarning: ast.Num is deprecated and will be removed in Python 3.14; use ast.Constant instead
      <string>:119: DeprecationWarning: ast.NameConstant is deprecated and will be removed in Python 3.14; use ast.Constant instead
      <string>:106: DeprecationWarning: Attribute s is deprecated and will be removed in Python 3.14; use value instead
      <string>:110: DeprecationWarning: Attribute n is deprecated and will be removed in Python 3.14; use value instead
      test_ruamel_yaml.c
      Vytv ýˇ se k˘d.
      Vytv ýenˇ k˘du se dokonźilo.
      C:\Users\Pavel\AppData\Local\Temp\pip-build-env-uosez9pj\overlay\Lib\site-packages\setuptools\dist.py:681: SetuptoolsDeprecationWarning: The namespace_packages parameter is deprecated.
      !!

              ********************************************************************************
              Please replace its usage with implicit namespaces (PEP 420).

              See https://setuptools.pypa.io/en/latest/references/keywords.html#keyword-namespace-packages for details.
              ********************************************************************************

      !!
        ep.load()(self, ep.name, value)
      sys.argv ['setup.py', 'bdist_wheel', '--dist-dir', 'C:\\Users\\Pavel\\AppData\\Local\\Temp\\pip-wheel-um2kqstr\\.tmp-zde2ynnq']
      test compiling C:\Users\Pavel\AppData\Local\Temp\tmp_ruamel_x29afh1w\test_ruamel_yaml.c -> test_ruamel_yaml OK
      running bdist_wheel
      running build
      running build_py
      creating build
      creating build\lib.win-amd64-cpython-312
      creating build\lib.win-amd64-cpython-312\ruamel
      copying .ruamel\__init__.py -> build\lib.win-amd64-cpython-312\ruamel
      creating build\lib.win-amd64-cpython-312\ruamel\yaml
      copying .ruamel\yaml\__init__.py -> build\lib.win-amd64-cpython-312\ruamel\yaml
      creating build\lib.win-amd64-cpython-312\ruamel\yaml\clib
      copying .\__init__.py -> build\lib.win-amd64-cpython-312\ruamel\yaml\clib
      copying .\LICENSE -> build\lib.win-amd64-cpython-312\ruamel\yaml\clib
      running build_ext
      building '_ruamel_yaml' extension
      creating build\temp.win-amd64-cpython-312
      creating build\temp.win-amd64-cpython-312\Release
      "C:\Program Files (x86)\Microsoft Visual Studio\2022\BuildTools\VC\Tools\MSVC\14.40.33807\bin\HostX86\x64\cl.exe" /c /nologo /O2 /W3 /GL /DNDEBUG /MD "-IC:\Program Files\Python312\include" "-IC:\Program Files\Python312\Include" "-IC:\Program Files (x86)\Microsoft Visual Studio\2022\BuildTools\VC\Tools\MSVC\14.40.33807\include" "-IC:\Program Files (x86)\Microsoft Visual Studio\2022\BuildTools\VC\Auxiliary\VS\include" "-IC:\Program Files (x86)\Windows Kits\10\include\10.0.22621.0\ucrt" "-IC:\Program Files (x86)\Windows Kits\10\\include\10.0.22621.0\\um" "-IC:\Program Files (x86)\Windows Kits\10\\include\10.0.22621.0\\shared" "-IC:\Program Files (x86)\Windows Kits\10\\include\10.0.22621.0\\winrt" "-IC:\Program Files (x86)\Windows Kits\10\\include\10.0.22621.0\\cppwinrt" /Tc_ruamel_yaml.c /Fobuild\temp.win-amd64-cpython-312\Release\_ruamel_yaml.obj
      _ruamel_yaml.c
      C:\Users\Pavel\AppData\Local\Temp\pip-install-3zswul_l\ruamel-yaml-clib_cb1357e752e94342b75128791d2fbf97\_ruamel_yaml.h(10): warning C4005: PyString_CheckExact: pýedefinov nˇ makra
      _ruamel_yaml.c(624): note: zkontrolujte pýedchozˇ definici "PyString_CheckExact"
      _ruamel_yaml.c(2060): warning C4090: =: odliçn‚ kvalifik tory const
      _ruamel_yaml.c(3590): warning C4113: int (__cdecl *)(void *,char *,int,int *) se liçˇ od: yaml_read_handler_t (__cdecl *) v seznamech parametr….
      _ruamel_yaml.c(4067): warning C4267: funkce: Pýevod z: size_t na: int, m…§e dojˇt ke ztr tŘ dat.
      _ruamel_yaml.c(4165): warning C4267: funkce: Pýevod z: size_t na: int, m…§e dojˇt ke ztr tŘ dat.
      _ruamel_yaml.c(4300): warning C4267: funkce: Pýevod z: size_t na: int, m…§e dojˇt ke ztr tŘ dat.
      _ruamel_yaml.c(4310): warning C4267: funkce: Pýevod z: size_t na: int, m…§e dojˇt ke ztr tŘ dat.
      _ruamel_yaml.c(4320): warning C4267: funkce: Pýevod z: size_t na: int, m…§e dojˇt ke ztr tŘ dat.
      _ruamel_yaml.c(4382): warning C4267: funkce: Pýevod z: size_t na: int, m…§e dojˇt ke ztr tŘ dat.
      _ruamel_yaml.c(4392): warning C4267: funkce: Pýevod z: size_t na: int, m…§e dojˇt ke ztr tŘ dat.
      _ruamel_yaml.c(4402): warning C4267: funkce: Pýevod z: size_t na: int, m…§e dojˇt ke ztr tŘ dat.
      _ruamel_yaml.c(5158): warning C4267: funkce: Pýevod z: size_t na: int, m…§e dojˇt ke ztr tŘ dat.
      _ruamel_yaml.c(5168): warning C4267: funkce: Pýevod z: size_t na: int, m…§e dojˇt ke ztr tŘ dat.
      _ruamel_yaml.c(5178): warning C4267: funkce: Pýevod z: size_t na: int, m…§e dojˇt ke ztr tŘ dat.
      _ruamel_yaml.c(5221): warning C4267: funkce: Pýevod z: size_t na: int, m…§e dojˇt ke ztr tŘ dat.
      _ruamel_yaml.c(5231): warning C4267: funkce: Pýevod z: size_t na: int, m…§e dojˇt ke ztr tŘ dat.
      _ruamel_yaml.c(5241): warning C4267: funkce: Pýevod z: size_t na: int, m…§e dojˇt ke ztr tŘ dat.
      _ruamel_yaml.c(8139): warning C4267: funkce: Pýevod z: size_t na: int, m…§e dojˇt ke ztr tŘ dat.
      _ruamel_yaml.c(8149): warning C4267: funkce: Pýevod z: size_t na: int, m…§e dojˇt ke ztr tŘ dat.
      _ruamel_yaml.c(8159): warning C4267: funkce: Pýevod z: size_t na: int, m…§e dojˇt ke ztr tŘ dat.
      _ruamel_yaml.c(8202): warning C4267: funkce: Pýevod z: size_t na: int, m…§e dojˇt ke ztr tŘ dat.
      _ruamel_yaml.c(8212): warning C4267: funkce: Pýevod z: size_t na: int, m…§e dojˇt ke ztr tŘ dat.
      _ruamel_yaml.c(8222): warning C4267: funkce: Pýevod z: size_t na: int, m…§e dojˇt ke ztr tŘ dat.
      _ruamel_yaml.c(11034): warning C4267: funkce: Pýevod z: size_t na: int, m…§e dojˇt ke ztr tŘ dat.
      _ruamel_yaml.c(11044): warning C4267: funkce: Pýevod z: size_t na: int, m…§e dojˇt ke ztr tŘ dat.
      _ruamel_yaml.c(11054): warning C4267: funkce: Pýevod z: size_t na: int, m…§e dojˇt ke ztr tŘ dat.
      _ruamel_yaml.c(11490): warning C4267: funkce: Pýevod z: size_t na: int, m…§e dojˇt ke ztr tŘ dat.
      _ruamel_yaml.c(11500): warning C4267: funkce: Pýevod z: size_t na: int, m…§e dojˇt ke ztr tŘ dat.
      _ruamel_yaml.c(11510): warning C4267: funkce: Pýevod z: size_t na: int, m…§e dojˇt ke ztr tŘ dat.
      _ruamel_yaml.c(11943): warning C4267: funkce: Pýevod z: size_t na: int, m…§e dojˇt ke ztr tŘ dat.
      _ruamel_yaml.c(11953): warning C4267: funkce: Pýevod z: size_t na: int, m…§e dojˇt ke ztr tŘ dat.
      _ruamel_yaml.c(11963): warning C4267: funkce: Pýevod z: size_t na: int, m…§e dojˇt ke ztr tŘ dat.
      _ruamel_yaml.c(12434): warning C4267: funkce: Pýevod z: size_t na: int, m…§e dojˇt ke ztr tŘ dat.
      _ruamel_yaml.c(12444): warning C4267: funkce: Pýevod z: size_t na: int, m…§e dojˇt ke ztr tŘ dat.
      _ruamel_yaml.c(12454): warning C4267: funkce: Pýevod z: size_t na: int, m…§e dojˇt ke ztr tŘ dat.
      _ruamel_yaml.c(12497): warning C4267: funkce: Pýevod z: size_t na: int, m…§e dojˇt ke ztr tŘ dat.
      _ruamel_yaml.c(12507): warning C4267: funkce: Pýevod z: size_t na: int, m…§e dojˇt ke ztr tŘ dat.
      _ruamel_yaml.c(12517): warning C4267: funkce: Pýevod z: size_t na: int, m…§e dojˇt ke ztr tŘ dat.
      _ruamel_yaml.c(13097): warning C4267: funkce: Pýevod z: size_t na: int, m…§e dojˇt ke ztr tŘ dat.
      _ruamel_yaml.c(13107): warning C4267: funkce: Pýevod z: size_t na: int, m…§e dojˇt ke ztr tŘ dat.
      _ruamel_yaml.c(13117): warning C4267: funkce: Pýevod z: size_t na: int, m…§e dojˇt ke ztr tŘ dat.
      _ruamel_yaml.c(13578): warning C4267: funkce: Pýevod z: size_t na: int, m…§e dojˇt ke ztr tŘ dat.
      _ruamel_yaml.c(13588): warning C4267: funkce: Pýevod z: size_t na: int, m…§e dojˇt ke ztr tŘ dat.
      _ruamel_yaml.c(13598): warning C4267: funkce: Pýevod z: size_t na: int, m…§e dojˇt ke ztr tŘ dat.
      _ruamel_yaml.c(13725): warning C4267: funkce: Pýevod z: size_t na: int, m…§e dojˇt ke ztr tŘ dat.
      _ruamel_yaml.c(13735): warning C4267: funkce: Pýevod z: size_t na: int, m…§e dojˇt ke ztr tŘ dat.
      _ruamel_yaml.c(13745): warning C4267: funkce: Pýevod z: size_t na: int, m…§e dojˇt ke ztr tŘ dat.
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

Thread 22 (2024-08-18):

USB-C to use it as standalone?

MrSpoocy, 2024-08-18:
Hello Sasa,

I am currently looking for a fan controller for my server cabinet and later for my living room cabinet. Unfortunately it is not possible to use a SATA power connector. I have seen that you already had a version with a DC-Jack connector. My question is, is it possible to swap the Micro-USB for USB-C with PD? So that it can be used for programming and power supply? It would still be possible to use it directly with the mainboard (https://www.ebay.de/itm/126257997569)

I plan to use ESP-Home as the firmware, as this now also supports the RP2040.

Kind regards Manuel

SasaKaranovic, 2024-09-04:
Hey @MrSpoocy !

I have two new version of OpenFAN coming up soon. Both of them will be stand-alone and work over WiFi.

In the meantime, you can also buy DC-to-SATA power adapters (Quick search on AliExpress gives a ton of options, see [here](https://www.aliexpress.com/w/wholesale-dc-to-sata-power.html))

p.s. Regarding USB-C PD; I think that the cable/adapter you linked is still USB2.0 without PD, it just has USB-C connector, so that would not work with the USB-C PD. Also from what I could tell, for some reason 12V on the USB-C PD is not really that popular. The 9V and 15V are way more common, but obviously don't work that well for our use case.

p.s. Sorry about late reply. I was away on vacation. :)

osnabrugge, 2024-09-04:
@SasaKaranovic what about PoE?  Has there been enough interest to build support for it?  That might also be a good solution for  @MrSpoocy if you have a PoE switch in your cabinet.

@SasaKaranovic I almost was about to buy a unit or two today but came across your blog about these new models.  Also, I noticed we live in the same city, I assume your storefront is direct from China, there's no way that I can transact locally to avoid to currency exchange and long shipping times / fees?

SasaKaranovic, 2024-09-05:
Hey @osnabrugge!

The PoE idea was considered at some point but I'm not sure how ubiquitous PoE is these days and how willing people are to "waste"/allocate some of that PoE budget to the fans. Honestly it would not be too difficult to built the PoE version but I suspect it would bloat the price and also make the product (even) more niche than it is right now. :\

You are correct, boards are produced and shipped from China so unfortunately I don't have any stock with me. Only a few prototypes and "beta" units.

Manufacturing these boards (sourcing, fabrication, programming, testing, QA etc) takes "a long time" so I don't generally like to announce/hype things before everything is completed and I have them in stock and they are ready to go. But I guess I already spilled the beans on the two additional versions of the OpenFAN so I might as well give some context. :)

- Active: OpenFAN is the solution if you need to control up to 10x PWM fans in your PC/server using SATA power and control over USB (and/or network using the software). This solution will continue to exist along with the new ones since they have different use-cases.
- Being manufactured. Available: ~end of September 2024: OpenFAN Micro is a version that controls single 5V or 12V PWM fan over WiFi and is powered from USB (no PD required)
- Not being manufactured. Available: TBD: OpenFAN WiFi is a version that controls up to 5x 5V or 12V PWM fans over WiFi and is using DC barrel jack for power.

OpenFAN Micro is close to being released so I will soon make a video explaining how it works, where it can be used and so on. Similar to what I did with the original OpenFAN.

Feel free to email me if you need more information on these or have more questions. :)

MrSpoocy, 2024-09-05:
Oh, I think my link was a bit misleading, this cable should only be for people who want to connect the controller further to their mainboard.

However, I think that USB-C PD with a “step down” is better than a DC jack. Good USB-C power supply are much more plentiful and easier to find (https://www.amazon.de/dp/B0CFF813QC). If you opt for USB-C PD, it should be compatible with the full standard (e.g step up for a original https://www.amazon.de/dp/B0CM46P7MC).

osnabrugge, 2024-09-06:
# Power over Ethernet (PoE) and USB-C Power Delivery (PD) for Home Labs

@SasaKaranovic thanks for your hard work and awesome update! I know a large community that makes use of PoE in their home labs (i.e. SBCs, APs, Cameras) and I'd be happy to introduce you to the originator of this project/discord group, I showed him your video last week and he found your project quite interesting. The group contributes to a community driven template that automates deployment(s) of a GitOps workflow including the setup of a k3s cluster that could be a single node on an SBC or as many nodes and platforms as you desire (so long as master nodes deployed meets HA requirements for quorum) thus strongly supports true open-source and certainly prefer free/low-cost solutions.

It might be possible through add-on modules to satisfy alternate power sources while keeping the original fan controller kit unmodified. However, it depends on whether the base board is extensible and able to handle the additional wattage. Otherwise, a V2 base board would be required to still meet the project's goals of keeping base cost low.

Using Power over Ethernet (PoE) and USB-C Power Delivery (USB-C PD) in home lab environments has both advantages and disadvantages. Add-on modules could be designed for specific power sources and/or a universal add-on to support SATA, USB-C PD, and PoE to satisfy @MrSpoocy's idea as well.

## Pros, Cons, and Use Cases for Supporting PoE and USB-C PD

- **PoE**
  - **Advantages**:
    - Greater distance (up to 100 meters)
    - Centralized power delivery control through the switch
    - Single Ethernet cable for both power and data, simplifying remote management.
  - **Disadvantages**:
    - Requires detailed installation and configuration documentation
    - Requires safety measures due to varying power standards (15W - 100W) that are non-interoperable.
  - **Use Case**:
    - Ideal for environments with existing PoE switch deployments
    - Existing/Desired solution to centrally manage other PoE devices already (e.g., AP, SBC, Camera).

- **USB-C PD**
  - **Advantages**:
    - Higher wattage (100W - 260W)
    - Automatic detection of the USB-C version and its corresponding power delivery limits
    - Reduced need for additional documentation and safety measures
  - **Disadvantages**:
    - Limited to 3 meters
    - Requires multiple cables or Wi-Fi for remote management
    - Lacks centralized management for multiple devices
  - **Use Case**:
    - Suitable for smaller environments without the need for remote access or centralized management
    - Especially useful for modern desktops with internal USB-C headers.

## Next Steps

Instead of hijacking this thread any further (sorry @MrSpoocy but I hoped that this message helps amplify supporting your use case as well), should I open a new issue, contact you privately through a real-time channel of your preference or via email as you suggested?

SasaKaranovic, 2024-09-07:
@MrSpoocy I agree that USB-C PD (and potential step-down) is a good idea.
However in practice I think it would be a mess due to different PD chargers have different set of voltages that they support.
This mess is created mainly because there is no "certification" for PD, and anyone who has any voltage other than 5V labels their charger as PD (even the cheap 5V/9V only phone chargers).

You could definitely get one that works well and has the voltage you need, but there is inevitably going to be a group of people who are going to be asking why their PD charger does not work. (So advertising it as USB-C PD could potentially be "misleading"?)

Also if USB-C is used for communication as well, then there is a problem if your motherboard/PC does not have PD, because then you can't power and communicate with the board using the same cable.

@osnabrugge Feel free to email me or open a new issue, either/both are fine with me.
For USB-C PD the above concern is the main issue. USB-C PD is not that well standardised (ie. which voltages must be supported) and could cause confusion/problems for some users.

The PoE version is interesting because there is one single cable for both power and data.
But depending on the fans attached you could easily take 10-15W out of your PoE budget.
Also there are different PoE standards that might increase the cost and complexity of the board if we opt to support all of them.

Keep in mind that WiFi edition already has only one cable for power and that's it.
And users could use a a cheap DC adaptor for power everything or even get a PoE-to-DC adaptor.

Closed 2024-09-29.

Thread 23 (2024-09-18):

zero rpm showing

russellevans, 2024-09-18:
I have purchased the openfan controller from you (Order #1085)....I live in the UK and with shipping costs it was expensive but I was happy if it did the job.

When I plug the fans in they turn for a moment and stop
There is two header where a fan runs but non of the others make the fans turn.
(These are 4 wire fans but if I only plug in three wires the fan does run)

I was seeing RPM on the self hosted web page but now everything shows as zero

I am using noctua NF-A14 & NF-A12x25 fans
The host is a Pi 4 and locally built the docker image to get things to work

My guess is I have a bad board
(Maybe I could of damaged it but that does not explain why only two headers ran fans out of the box)

The container logs seem clean but I am not an expert

What do you recommend to do next?  Will you send a replacement board?

`Sep 18 2024 06:19:43.349 pid:7 FanCommander.py          103 DEBUG 	SN: DE615CB147712230
Sep 18 2024 06:19:43.349 pid:7 FanCommander.py          104 DEBUG 	VID:11914 PID:10
Sep 18 2024 06:19:43.349 pid:7 FanCommander.py          105 DEBUG 	Location: 1-1.4:1.0
Sep 18 2024 06:19:43.349 pid:7 FanCommander.py          106 DEBUG 	Interface: Board CDC
Sep 18 2024 06:19:43.349 pid:7 FanCommander.py          108 DEBUG Using 'OpenFan - Board CDC' as Fan Controller COM port
Sep 18 2024 06:19:43.349 pid:7 webserver.py             302 INFO  Using COM port `/dev/ttyACM0 - OpenFan - Board CDC` (Found through USB VID:PID).
Sep 18 2024 06:19:43.349 pid:7 webserver.py             304 INFO  Fan Controller port: /dev/ttyACM0 - OpenFan - Board CDC
Sep 18 2024 06:19:43.352 pid:7 serial_driver.py          43 DEBUG Serial driver initialized with
Sep 18 2024 06:19:43.352 pid:7 serial_driver.py          44 DEBUG -- flush_on_write: 'True'
Sep 18 2024 06:19:43.352 pid:7 serial_driver.py          45 DEBUG -- timeout: '2'
Sep 18 2024 06:19:43.352 pid:7 webserver.py             334 INFO  Karanovic Research OpenFan - Starting API server
Sep 18 2024 06:19:43.357 pid:7 webserver.py             339 INFO  Listening on port 3000
Sep 18 2024 06:18:09.763 pid:7 webserver.py             145 INFO  Request:STATUS
Sep 18 2024 06:18:09.763 pid:7 FanCommander.py           24 DEBUG CMD:0 Data: None
Sep 18 2024 06:18:09.763 pid:7 FanCommander.py           25 DEBUG Sending `>00`
Sep 18 2024 06:18:09.809 pid:7 FanCommander.py           31 DEBUG [0001131594][I][HCOMM] >00
Sep 18 2024 06:18:09.809 pid:7 FanCommander.py           31 DEBUG [0001131594][D][HCOMM] host_comm_tick: Start character found (Len=2)
Sep 18 2024 06:18:09.809 pid:7 FanCommander.py           31 DEBUG [0001131594][D][HCOMM] host_comm_parse_package
Sep 18 2024 06:18:09.809 pid:7 FanCommander.py           31 DEBUG [0001131594][D][HCOMM] A=00 H:0x00
Sep 18 2024 06:18:09.809 pid:7 FanCommander.py           31 DEBUG [0001131594][D][HCOMM] CMD_FAN_ALL_GET_RPM
Sep 18 2024 06:18:09.809 pid:7 FanCommander.py           31 DEBUG <00|00:0000;01:0000;02:0000;03:0000;04:0000;05:0000;06:0000;07:0000;08:0000;09:0000;
Sep 18 2024 06:18:09.810 pid:7 FanCommander.py           33 DEBUG Response: '<00|00:0000;01:0000;02:0000;03:0000;04:0000;05:0000;06:0000;07:0000;08:0000;09:0000;'
Sep 18 2024 06:18:09.810 pid:7 FanCommander.py           46 DEBUG {0: 0, 1: 0, 2: 0, 3: 0, 4: 0, 5: 0, 6: 0, 7: 0, 8: 0, 9: 0}`

SasaKaranovic, 2024-09-21:
Hey @russellevans

Sorry about late reply. Please send an email to shop@sasakaranovic.com and we will resolve this issue ASAP.
GitHub issues are more for community contributions/discussions etc.

Also I understand and agree that shipping prices are high. Unfortunately, at the moment those are the "best" rates I can get with the current shipping company...
I am a single person sending a few packets a month, so understandably they are not going to fight for a drop in a bucket.
And to be honest, I don't want to "mislead" people by spiking up the prices and claiming that shipping is "free", because then if you buy multiple items, you pay that inflated (shipping) price multiple times...

Closed 2024-10-12.

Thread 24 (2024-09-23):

PoE support for OpenFanController

osnabrugge, 2024-09-23:
# New Issue: PoE support for OpenFanController

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

_Originally posted by [@SasaKaranovic](https://github.com/SasaKaranovic/OpenFanController/issues/22#issuecomment-2335007194)_

@SasaKaranovic sorry for dropping the ball on this one, I have my hands full with a lot of projects at the moment. I decided to create a separate issue to allow the other issue to focus on USB-C PD.

## Issue Description

The goal is to determine if there is a market audience that would be interested in a PoE based solution vs. the complexity of implementing either a new board solution or if possible an add-on board so that existing users can benefit with a marginal cost to upgrade to PoE.

### Alternate Solutions (you proposed)

Regarding your comment, quote from [issue #22](https://github.com/SasaKaranovic/OpenFanController/issues/22#issuecomment-2335007194):

> Keep in mind that WiFi edition already has only one cable for power and that's it.
> And users could use a a cheap DC adaptor for power everything or even get a PoE-to-DC adaptor.

This will not meet the requirements, at least for HomeLab users. The target audience may include other groups and/or use cases. HomeLab users are trying to follow recommended practices around IoT devices, Wi-Fi optimization, etc.

Most users will typically have a separate VLAN for devices similar to your project. They try to use physical cables wherever possible for security, reliability, and performance reasons.

### Market Size

The reason I can confidently say that there is at least a small market (and could be larger even for this use case) is because some HomeLab users will have PoE switches to run RTSP cameras to software like Frigate, Zoneminder, Shinobi, Motion, motionEyeOS, Yawcam, etc.

They should have at least 802.3af / PoE+ (802.3at / PoE++ is relatively new and expensive). Even with PoE+, each ethernet cable is capable of delivering up to 30W, which is more than enough to power 10 fans as long as they aren't planning to deploy many high AMP fans (can't think of a practical use case).

Of course, their switch needs to have power capacity for how many controllers and fans they deploy. How I came to this conclusion is based on the following:

- [Home Operations Discord Channel](https://discord.gg/home-operations) has over 1000 active members online at any time.
That is just one example of software that is popular with this community, and I'm sure there are many other similar tools and applications that could benefit from PoE support.
- [kubesearch.dev](https://kubesearch.dev/) is a search page the community made that indexes all who have tagged and repos they are running, which is super helpful to get inspiration, solutions, etc. and see what others are running.
  - [As an example, this shows](https://kubesearch.dev/hr/ghcr.io-bjw-s-helm-app-template-frigate) there are at least 26 active members running Frigate which means they have PoE switches for their cameras. Wi-Fi cameras will drain the battery far too quickly and also chew up Wi-Fi bandwidth exactly when you need it most. There are also those who don't tag themselves or use standalone NVR solutions outside of their k3s cluster.

That is just one example of software that is popular with this community, and the founder of this community @onedr0p even mentions a few of them in the template. I'm sure there are many other

## Justification

That is just one example of software that is popular with this community, and the founder of this community @onedr0p mentions a few of them in the [related projects section near the end of the template](https://github.com/onedr0p/cluster-template#-related-projects). Personally, I believe there is appetite, but it will be difficult to quantify without spreading the word around to gauge interest over a broader population. I'm sure there are many other similar communities with similar needs and other use cases that would justify having a that a user must already have a PoE switch.

## Assistance

I would be happy to assist you, but my skills at low level hardware and coding are not as strong as you, so I can assist with perhaps getting a poll to gauge interest, help with QA/Beta testing, brainstorming, etc.

Will it be possible to create an add-on module?

1. Address any other concerns you may have
2. Determine if there is a market for PoE
3. Determine if it is possible to create an add-on module
4. Determine if it is possible to do a new board
5. If the above are possible, determine the cost of development

Looking forward to your thoughts on this and whether we should explore this further.

P.S. I ordered one for now and hope it will work with a Supermicro server. I heard that some others tried boxed brand solutions and ended up frying them. There are 7 hot-swappable fans that draw 0.6 amps each, so I'm not quite sure how they fried their controllers.

Closed 2024-10-14.

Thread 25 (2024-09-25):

Update firmware on GitHub

GewoonJaap, 2024-09-25:
A few weeks ago we chatted via e-mail about the new firmware for the latest revision of the openFAN boards. Could you also upload this firmware here on GitHub, so all the other users won't install out-dated firmware ;)

SasaKaranovic, 2024-09-26:
Thanks @GewoonJaap !
The firmware you received is not newer, it's the exact same, just modified for the revision of the board you received. :)

Closed 2024-09-26.

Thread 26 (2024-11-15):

Fan Input extension

anthony0030, 2024-11-15:
A feature that I thought of is to use one or both of the expansions ports to be able to put a fan input from the motherboard. This will send data back to the motherboard emulating a fan and get data from the fan header on the motherboard to be able to set a custom fan speed from the data coming from the motherboard, especially useful if you only have one or two fan headers and want to control different fans.

SasaKaranovic, 2024-11-17:
Thanks for the suggestion @anthony0030 !

This is a neat idea, but I think it does not align with this project and it's somewhat redundant.
We want to decouple fan control from hardware, software/OS etc.

If I did not understand you suggestion, feel free to correct me. But this feature would create a dependency between OpenFAN and the motherboard and how the motherboard drives the fan, what software you have to use to create those fan curves etc.

With OpenFAN, the idea is that you have critical fan control (ie. CPU fan) connected directly to the motherboard and then everything else i controlled by the OpenFAN.

anthony0030, 2024-11-18:
Good morning @SasaKaranovic,

Thank you for getting back to me.

I was unaware of:
> With OpenFAN, the idea is that you have critical fan control (ie. CPU fan) connected directly to the motherboard and then everything else i controlled by the OpenFAN.

I was trying to explain the functionality of the [na-fc1](https://noctua.at/en/na-fc1) by noctua.
It basically sits between the motherboard and the fans and you set the potentiometer to 50% and it will reduce the fan speed by that much while still providing fan data to the motherboard. There would be no additional software in my example just another option in your existing software to be able to accept the fan output from the motherboard and reduce it when it gets to the fan, Thanks again for your response and great videos!

anthony0030, 2024-11-20:
@SasaKaranovic thank you for taking the time to clarify this for me.

I look forward to doing a project that uses this fan controller. It looks like an amazing project, and the PCB looks really cool.

Closed 2024-11-20.

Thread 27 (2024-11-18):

Alert pin in FW

ledadrian, 2024-11-18:
I wanted to try this with a Seeed Studio XIAO RP2040, but I noticed the EMC2305 has alert pins connected to GPIO 11 and GPIO 17. I was looking at the FW to change the pins becuase the seeed studio board does not breakout those pins. I was unable to find those pins being used in the FW. Are the alerts being used in this version?

SasaKaranovic, 2024-11-20:
You can program the EMC2305 to create alerts for various conditions.
This feature is not used right now.

Closed 2024-11-20.

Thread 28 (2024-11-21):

Questions about lm-sensors, power usage, and firmware modifications of PCB-revisions

libr3, 2024-11-21:
I have become interested in the project and I'm considering whether to purchase a pre-built version, but I have four questions:

1. Does the project work with lm-sensors [1]? If not, I think it would be a good idea to add compatibility since many programs related to controlling fans rely on it, such as fan2go [2], which I particularly like.

2. How many watts can each fan use? One of the products competing with this project would be Corsair devices, which also have official kernel support and work with lm-sensors (like the Corsair Commander Core XT), but Corsair devices only support up to 6 fans, and their firmware is proprietary.

3. I usually compile everything from source (I use Gentoo, a GNU/Linux distribution that, unlike most, is not binary-based): I’ve seen in another issue that you are now sending new revisions of the PCB [3], which have modified firmware because it's adapted to that revision. You mentioned to the user that the only change was adapting it to their hardware revision, but that implies a modification. I'm seriously concerned that when you send me the new revision, I won’t be able to compile from source and install the firmware because the adapted source code for the revision you are sending now is not available in this repository. It would be great if you could publish that modification so anyone—not just me—who has a different revision of the board could modify and reinstall it from source, just as I would do myself. I plan to recompile and reinstall the firmware once I receive the pre-built device, so it would be helpful if you could even release the source code for those revisions to allow me to do so.

4. Do you have an ETA for when you'll release the version with a USB Type-C port? I wouldn't mind paying a bit more for it to have a Type-C port, or finding the cable myself if it has that port and the cable is expensive.

[1] https://github.com/lm-sensors/lm-sensors
[2] https://github.com/markusressel/fan2go
[3] https://github.com/SasaKaranovic/OpenFanController/issues/25#issuecomment-2375801323

SasaKaranovic, 2024-11-30:
Hey @libr3,

Thanks for the great suggestion. Unfortunately OpenFAN Controller does NOT have lm_sensors integration at the moment.
The maximum current per fans sounds like an easy question to answer but it's not.
Short answer is **by design**, OpenFAN Controller could deliver around 1-1.5A to each fan. Key word being **could**.
However you have to keep in mind that there are many links in the power-supply chain. Depending on your power supply, it would usually supports around ~3-4A (maximum/total) on your SATA power, which then gets divided to however many fans you have. This means that while OpenFAN could easily provide 1A to all 10 fans, your power supply probably can't supply 10A on the SATA power cable, so the limit would be whatever your power supply can **safely** provide.

Also, while I understand what you mean, in my mind I don't think this project is "competing" with anyone/anything. Especially not with products made by billion dollar companies. :)
It's just something that I built for myself and thought others might find useful.
With that said, if you have any doubts or concerns, I would recommend getting a different product that makes you more comfortable.

Closed 2024-11-30.

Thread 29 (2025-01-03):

custom default fan profile

matdibu, 2025-01-03:
Thank you for making this, it's working perfectly!

That being said, would it be possible to embed a custom default fan profile directly into the board?

I've figured out exactly where I like my fans to be at, but it's a bit annoying having to rely on the host OS (I dual boot, so I have to configure it twice) to apply that profile.

I'd be much happier if I could flash/hardcode my settings as the default profile.

SasaKaranovic, 2025-01-03:
Hey @matdibu !

Ideally you would not want to run the OpenFAN Controller in a "headless" (without PC/SW) mode.

If you are dual booting, you could share the config file in both OS-es, for example share the SW directory or just the config file.
And then have the software re-apply the profile on boot without any interaction on your side.

If you really don't want to run the software, you could create a script that on-boot sends fan profile and that's it.
It's up to you how you want to use your board, but I would highly recommend running the software and actively adjusting the fan speed based on temperature and/or load. :)

matdibu, 2025-01-09:
This is what I settled on: https://codeberg.org/mateidibu/nix-config/src/commit/1cb80413e8337da7e914414f50a915c73c36c45e/hosts/x570/services/containers/openfan.nix

I start the container and then use the API to create and apply a profile

Closed 2025-01-09.

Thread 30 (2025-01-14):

Some questions. Can it be used wirelessly and max amps

LoLo2207, 2025-01-14:
Hi, I just found about this controller thanks to a Reddit [reply ](https://www.reddit.com/r/esp32/comments/1i0i4q6/comment/m75omac/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) because I was trying to do something similar myself but I have no experience designing PCBs

I have an external radiator and this would be perfect if I could use it wirelessly. Does it need to be always plugged in to the USB or the configuration website and FanControl works through WiFi? I was planning on reporting the RPMs back to the host using ESP-now on my case and having another ESP32 inside the computer and then writing the integration with FanControl, which I also use.

Another question, what's the amperage on the headers? Have you tested it with any watercooling pump? I need only 2 headers, one for 9 fans (about 1A total) and another one for the pump (max 2A at 100%)

BTW This project would be very interesting to the watercooling (and the MORA radiator) folks in reddit

SasaKaranovic, 2025-01-18:
Hey @LoLo2207

You could use this board wirelessly but not on it's own. For example you could hook it up to Raspberry Pi (any would work).
BTW, the board uses standard USB connector for communication, so even if your setup is outside of your PC case, you could just run a USB cable back to your PC and it should work. For power you can get one of external SATA power adapters.

> Another question, what's the amperage on the headers? Have you tested it with any watercooling pump? I need only 2 headers, one for 9 fans (about 1A total) and another one for the pump (max 2A at 100%)

This question is not very easy to answer. There are many limiting factors, like your power supply, cables it uses, SATA connector, peak vs average current use etc. With that said, your maximum power draw will be limited by the "weakest link" in this chain.
The traces on the PCB should be able to easily handle 3A that you mentioned, but make sure everything else in the chain can do the same.
I have _not_ tested the board using any watercooling pumps (I don't have access to any). And honestly I think it might not work well with them, mainly because waterpumps and fans behaviour (RPM, TACH etc) will be much different than fan.

> BTW This project would be very interesting to the watercooling (and the MORA radiator) folks in reddit

Thank you! Great suggestion but I personally don't like when people shamelessly promote their projects/products or do it using puppet accounts, so because of this I won't post about it. But feel free to mention it or share your experience if you like.
My thoughts are that if something is good and worth mentioning, over time people will learn about it and share it with each other.

ThomasEg, 2025-01-22:
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

I was actually looking for this exact information aswell. I run a "whole rack watercooling system" and have some industrial Noctua-fans running outside the house. These run at 0,5A each at full tilt. I was wondering what the PCB traces was rated at for this reason. I wouldn't want to let out the magic smoke ;-) I think most waterpumps also run at max 0,5A from the fan-connector, if higher power is required they usually come with a SATA power connector aswell. It could be interesting to do a load-test to the PCB and check if there is any hotspots...got a thermal camera anyone? :-)

> > BTW This project would be very interesting to the watercooling (and the MORA radiator) folks in reddit
>
> Thank you! Great suggestion but I personally don't like when people shamelessly promote their projects/products or do it using puppet accounts, so because of this I won't post about it. But feel free to mention it or share your experience if you like. My thoughts are that if something is good and worth mentioning, over time people will learn about it and share it with each other.

I'm going to power one(maybe two) pumps through this board, hopefully. The pumps actually act quite like a fan, they accept PWM input and return actual RPM. How this RPM is then translated to to actual waterflow is another rabbithole not suiteable for this project ;-) But it is one of the things i hope to use the i2c port for...temperature and/or flow-sensor... Could be a series of add-ons for this board maybe? I would have ordered these from your shop if they were there... for now i just ordered one controller and see if i can make something work :-)

SasaKaranovic, 2025-01-23:
> I was actually looking for this exact information aswell. I run a "whole rack watercooling system" and have some industrial Noctua-fans running outside the house. These run at 0,5A each at full tilt. I was wondering what the PCB traces was rated at for this reason. I wouldn't want to let out the magic smoke ;-) I think most waterpumps also run at max 0,5A from the fan-connector, if higher power is required they usually come with a SATA power connector aswell. It could be interesting to do a load-test to the PCB and check if there is any hotspots...got a thermal camera anyone? :-)

From the design perspective, traces are 2.5mm thick and that should easily carry at least 4-5A.
This is for per fan row, so 4-5A for top 5 fans (1-5), and another 4-5A for 5 bottom fans (6-10).
Obviously I did **not** test this, it's just numbers that I get from the design and back of the napkin calculation.

>I'm going to power one(maybe two) pumps through this board, hopefully. The pumps actually act quite like a fan, they accept PWM input and return actual RPM. How this RPM is then translated to to actual waterflow is another rabbithole not suiteable for this project ;-) But it is one of the things i hope to use the i2c port for...temperature and/or flow-sensor... Could be a series of add-ons for this board maybe? I would have ordered these from your shop if they were there... for now i just ordered one controller and see if i can make something work :-)

I do not have a water cooled system, so I can't test this. Even fans are not all standardized when it comes to RPM calculation/indication, but most commercial ones would produce 2 impulses per revolution. I would expect pump and fan to have a different RPM response curve, so the PID algorithm that is used for achieving target RPM on a fan, might not be compatible with the water pump.

But with all that said... there is only one way to find out. :)

Closed 2025-02-13.

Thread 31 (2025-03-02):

Mounting options for PCB?

ThomasEg, 2025-03-02:
I ordered the fancontroller and i got another PCB revision than the one illustrated in the Readme.md and as the CAD-models in this repository. My revision only has 2 mounting holes, not 3.

I'm opening this issue in the hope that you might consider a couple of things in future revisions of the PCB.

In my opinion the PCB is way to size-optimized, introducing some unfortunate compromises. First off two mounting holes spaced very closely is problematic, 3 holes is manageable but 4 or maybe 5 would yield much more mounting options. The PCB being 5-10mm larger in both directions to allow for this is IMO a way better tradeoff.

Second issue: The mounting holes matches M3 screws which is perfect! However, there are traces running very close to the holes, especially one of the holes are problematic. In fact, so close that i don't think it is a good option to use ordinary steel-screws in the holes without isolating washers. I'm pretty sure that a slight mistake with the screw will result in a short. Again i think bigger pads and space around the holes to allow for mounting using regular screws is the better tradeoff than to minimizing the overall PCB.

SasaKaranovic, 2025-03-02:
Thanks @ThomasEg !
I'll add this to the list and keep it in mind for the future revisions of the board.

Closed 2025-03-11.

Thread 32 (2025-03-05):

Any models of the Latest Revision Hardware?

Senorgif2, 2025-03-05:
I received my openfan a few days ago, and I was planning on making a mount for it, but I cant seem to find any documentation or models of the latest PCB revision (June 2024).

ThomasEg, 2025-03-09:
Yeah, i've encountered the same issue. The enclosure here: https://github.com/SasaKaranovic/OpenFanController/blob/master/Enclosure/Bottom-PCB-Enclosure_by_Sam_Chan.3mf seems to be the new design, while the .step file and the Fusion360-file in the same folder seems to be an older design(3 holes vs. 2 holes for mounting). Maybe you can use the enclosure from Sam Chan to get started?

SasaKaranovic, 2025-03-11:
I have updated the [enclosure](https://github.com/SasaKaranovic/OpenFanController/tree/master/Enclosure) folder to include .step file of the board.
Also added another enclosure designed by Joe Dutson.

p.s. I don't know what kind of enclosure you are building and how precise/accurate your machines are, but I would say that for most (OpenFAN enclosure) use-cases, measuring from mesh or using calipers is more than accurate enough. Especially if you are 3D printing or laser-cutting an enclosure. :)

Senorgif2, 2025-03-11:
> I have updated the [enclosure](https://github.com/SasaKaranovic/OpenFanController/tree/master/Enclosure) folder to include .step file of the board. Also added another enclosure designed by Joe Dutson.
>
> p.s. I don't know what kind of enclosure you are building and how precise/accurate your machines are, but I would say that for most (OpenFAN enclosure) use-cases, measuring from mesh or using calipers is more than accurate enough. Especially if you are 3D printing or laser-cutting an enclosure. :)

Thank you very much! No doubt I would have been able to figure it out, I have done something like that before, but it also usually means printing a few failed prototypes first. I am waiting for a lot of other parts for this project so I wasn't in a huge hurry, and I'd rather do it the easy way haha

SasaKaranovic, 2025-03-12:
No argument there. If you have the CAD model it's obviously much easier to do the measurements and work around it.
But I was also joking that we are getting a bit "spoiled" by having so much access to raw CAD/data, that if one piece is missing, we start flipping tables and rebelling. 😂

Anyway, jokes aside, feel free to let me know if you have any issues with the model or need any additional support.

Closed 2025-03-11.

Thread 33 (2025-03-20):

Issues with self-made boards

Terrails, 2025-03-20:
Hey there. I have gotten 2 assembled boards with the files from `2023-10-28_2203_OpenFan_R03`. I only had to solder the SATA power connector manually and did that for both.

After flashing the `2023-09-29_OpenFAN_FW_01.uf2` firmware image, I thought everything went well as the LED on the boards started blinking. And both boards do indeed show up as "USB Composite Device" with two "USB Serial Device" in Device Manager on Windows. But after starting the Python Webserver I immediately got hit by a wall of errors. Specifically `emc230x_send_then_read: write error 0xFFFFFFFF`. I did also connect to both boards via PuTTY and they are constantly spewing errors like:
```
[0000327517][E][EMC230X] emc230x_send_then_read: write error 0x01
[0000327517][E][EMC230X] emc230x_send_then_read: read error 0x01
[0000327517][E][EMC230X] emc230x_send_then_read: write error 0x01
[0000327517][E][EMC230X] emc230x_send_then_read: write error 0x01
[0000327517][E][EMC230X] emc230x_send_then_read: read error 0x02
```
The read errors are not present when looking at the console output of Python Webserver, but it is only attempting to get the RPM of all fans. I assume the output in PuTTY console is what the firmware is doing in the background.

I am wondering what could be wrong with the boards? From a quick look at the `emc230x_send_then_read` function inside `emc230x.c` I do see that it throws an error when the status is non-zero, so I assume it expects `i2c_write_timeout_us` and `i2c_read_timeout_us` to return 0 bytes written/read when the error occurs to succeed?

Oh and by the way, I was wondering which logging library you use for the firmware as the files are not present in the repo. I do see that `tinyusb` is declared in `CMakeLists.txt`. There's also `Lib/Logger`, but I have no idea which library I should get for that in order to compile the firmware myself.

Thank you for this amazing project, I just hope that I can get it running.

Terrails, 2025-03-20:
> so I assume it expects i2c_write_timeout_us and i2c_read_timeout_us to return 0 bytes written/read when the error occurs to succeed?

It seems like this was the actual issue. I have just made all the checks only do their thing when `status <= 0`. I did have to remove all the references to logging in order to compile, so I do hope that the source files for those can be added

Terrails, 2025-09-01:
> [@Terrails](https://github.com/Terrails) have you had any progress on your issue? I'm also getting the exact same errors as you regarding emc230x_send_then_read read/write errors. Trying to build the Firmware but missing the Logger and tinyusb

Sorry for the late reply. I did get it to work and wrote my own Logger in a [branch of my fork](https://github.com/Terrails/OpenFanController/tree/firmware_updates). I also did some changes besides that to make it easier for development in VSCode. It has been running without issues in my unRAID server.

Closed 2025-04-10.

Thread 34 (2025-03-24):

Initial Setup Support

Tenorbro, 2025-03-24:
Out of the box, setup has been as expected with the new board. Im able to see the webpage and interact with the setting as seen in your YouTube demonstration.

I seem to be having issue with access the api. With a port scan, I can only see port 80 open, so I cant seem to go any further. May I have assistance for the next steps to access the api? Im looking to integrate into HomeAssistant. Thank you.

PORT     STATE  SERVICE
22/tcp   closed ssh
80/tcp   open   http
443/tcp  closed https
3000/tcp closed ppp
8080/tcp closed http-proxy

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

Closed 2025-03-31.

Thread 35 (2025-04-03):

Flashing Light

Yintiee, 2025-04-03:
Not so much a problem, everything seems to be working fine so far, but the card has a flashing white light on it, looks like the light says "ACT" on it.  Just want to know if this is normal.

Yintiee, 2025-04-03:
I also cant figure out how to get it into bootloader mode.  Ive tried pressing the boot button on board but it doesnt do anything.  Tried resetting it while holding the boot down, tried unplugging and replugging it.  Device never shows up in explorer.

Closed 2025-04-24.

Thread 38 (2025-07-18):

Unraid openfancontroller docker

Safwaniz911, 2025-07-18:
Jul 18 2025 10:32:43.497 pid:7 FanCommander.py           31 DEBUG [0001655166][E][EMC230X] emc230x_send_then_read: write error 0x01
Jul 18 2025 10:32:43.497 pid:7 FanCommander.py           31 DEBUG [0001655166][E][EMC230X] emc230x_send_then_read: write error 0x01
Uncaught exception GET /api/v0/fan/status (172.16.20.2)
HTTPServerRequest(protocol='http', host='172.16.30.169:3210', method='GET', uri='/api/v0/fan/status', version='HTTP/1.1', remote_ip='172.16.20.2')
Traceback (most recent call last):
  File "/usr/local/lib/python3.10/dist-packages/tornado/web.py", line 1788, in _execute
    result = method(*self.path_args, **self.path_kwargs)
  File "/mnt/OpenFan/webserver.py", line 147, in get
    rpm = self.handler.get_all_fan_rpm()
  File "/mnt/OpenFan/FanCommander.py", line 57, in get_all_fan_rpm
    return self._parse_fan_rpm(res)
  File "/mnt/OpenFan/FanCommander.py", line 38, in _parse_fan_rpm
    res = response.split("|")
AttributeError: 'bool' object has no attribute 'split'
500 GET /api/v0/fan/status (172.16.20.2) 5711.24ms
Jul 18 2025 10:32:43.499 pid:7 webserver.py             145 INFO  Request:STATUS
Jul 18 2025 10:32:43.499 pid:7 FanCommander.py           24 DEBUG CMD:0 Data: None
Jul 18 2025 10:32:43.499 pid:7 FanCommander.py           25 DEBUG Sending `>00`

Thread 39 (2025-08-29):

AttributeError: 'bool' object has no attribute 'split' on Raspberry Pi ARM

AlphaSoftwareInc, 2025-08-29:
Hello,

I have installed the Software via Docker on two different machines (Debian VM running on x64 and Raspberry Pi OS on Raspberry Pi 5 aarch64). On Debian it's running just fine but on Raspberry I get no RPM Speeds. Via the log I get this error message:

```
Aug 29 2025 18:59:47.296 pid:7 base_logger.py            59 INFO  Logging level: INFO
Aug 29 2025 18:59:47.305 pid:7 config.py                 49 DEBUG Server config:
Aug 29 2025 18:59:47.305 pid:7 config.py                 58 DEBUG {'hostname': 'localhost', 'port': 3000, 'communication_timeout': 1}
Aug 29 2025 18:59:47.305 pid:7 config.py                 60 DEBUG Hardware config:
Aug 29 2025 18:59:47.305 pid:7 config.py                 69 DEBUG {'port': None}
Aug 29 2025 18:59:47.305 pid:7 config.py                 71 DEBUG Fan profile config:
Aug 29 2025 18:59:47.305 pid:7 config.py                 80 DEBUG {'1000 RPM': {'type': 'rpm', 'values': [1000, 1000, 1000, 1000, 1000, 1000, 1000, 1000, 1000, 1000], 'name': '1000 RPM'}, 'MadMax': {'type': 'PWM', 'values': [100, 100, 100, 100, 100, 100, 100, 100, 100, 100], 'name': 'MadMax'}, '1200RPM': {'type': 'RPM', 'values': [1200, 1200, 1200, 1200, 1200, 1200, 1200, 1200, 1200, 1200], 'name': '1200RPM'}}
Aug 29 2025 18:59:47.305 pid:7 config.py                 83 DEBUG Fan aliases:
Aug 29 2025 18:59:47.305 pid:7 config.py                 92 DEBUG {0: 'Fan #1', 1: 'Fan #2', 2: 'Fan #3', 3: 'Fan #4', 4: 'Fan #5', 5: 'Fan #6', 6: 'Fan #7', 7: 'Fan #8', 8: 'Fan #9', 9: 'Fan #10'}
Aug 29 2025 18:59:47.305 pid:7 webserver.py             295 INFO  Using COM port `/dev/ttyACM0` (specified in `OPENFANCOMPORT` env variable).
Aug 29 2025 18:59:47.305 pid:7 webserver.py             304 INFO  Fan Controller port: /dev/ttyACM0
Aug 29 2025 18:59:47.307 pid:7 serial_driver.py          87 DEBUG Searching for COM port `/dev/ttyACM0`
Aug 29 2025 18:59:47.307 pid:7 serial_driver.py          89 DEBUG /dev/ttyACM0
Aug 29 2025 18:59:47.307 pid:7 serial_driver.py          90 DEBUG       Product: OpenFan
Aug 29 2025 18:59:47.307 pid:7 serial_driver.py          91 DEBUG       Desc: OpenFan - Board CDC
Aug 29 2025 18:59:47.307 pid:7 serial_driver.py          92 DEBUG       SN: DE6424128F7E2234
Aug 29 2025 18:59:47.307 pid:7 serial_driver.py          93 DEBUG       VID:11914 PID:10
Aug 29 2025 18:59:47.307 pid:7 serial_driver.py          94 DEBUG       Location: 3-1:1.0
Aug 29 2025 18:59:47.307 pid:7 serial_driver.py          95 DEBUG       Interface: Board CDC
Aug 29 2025 18:59:47.307 pid:7 serial_driver.py          97 DEBUG Using '/dev/ttyACM0' COM port
Aug 29 2025 18:59:47.309 pid:7 serial_driver.py          43 DEBUG Serial driver initialized with
Aug 29 2025 18:59:47.309 pid:7 serial_driver.py          44 DEBUG -- flush_on_write: 'True'
Aug 29 2025 18:59:47.309 pid:7 serial_driver.py          45 DEBUG -- timeout: '2'
Aug 29 2025 18:59:47.309 pid:7 webserver.py             334 INFO  Karanovic Research OpenFan - Starting API server
Aug 29 2025 18:59:47.310 pid:7 webserver.py             339 INFO  Listening on port 3000
Aug 29 2025 19:00:33.331 pid:7 webserver.py             257 DEBUG Requesting: None
Aug 29 2025 19:00:33.525 pid:7 webserver.py              53 INFO  Request:FANPROFILE_LIST
Aug 29 2025 19:00:33.532 pid:7 webserver.py             199 INFO  Request:GET ALL FAN Aliases
Aug 29 2025 19:00:34.544 pid:7 webserver.py             145 INFO  Request:STATUS
Aug 29 2025 19:00:34.544 pid:7 FanCommander.py           24 DEBUG CMD:0 Data: None
Aug 29 2025 19:00:34.544 pid:7 FanCommander.py           25 DEBUG Sending `>00`
Aug 29 2025 19:00:41.050 pid:7 serial_driver.py         145 ERROR Timeout occured (1756494041.0506754 > 1756494040.0444684)
Uncaught exception GET /api/v0/fan/status (192.168.1.60)
HTTPServerRequest(protocol='http', host='192.168.1.10:9000', method='GET', uri='/api/v0/fan/status', version='HTTP/1.1', remote_ip='192.168.1.60')
Traceback (most recent call last):
  File "/usr/local/lib/python3.10/dist-packages/tornado/web.py", line 1846, in _execute
    result = method(*self.path_args, **self.path_kwargs)
  File "/mnt/OpenFan/webserver.py", line 147, in get
    rpm = self.handler.get_all_fan_rpm()
  File "/mnt/OpenFan/FanCommander.py", line 57, in get_all_fan_rpm
    return self._parse_fan_rpm(res)
  File "/mnt/OpenFan/FanCommander.py", line 38, in _parse_fan_rpm
    res = response.split("|")
AttributeError: 'bool' object has no attribute 'split'
500 GET /api/v0/fan/status (192.168.1.60) 6508.55ms
Aug 29 2025 19:00:41.547 pid:7 webserver.py             145 INFO  Request:STATUS
Aug 29 2025 19:00:41.547 pid:7 FanCommander.py           24 DEBUG CMD:0 Data: None
Aug 29 2025 19:00:41.548 pid:7 FanCommander.py           25 DEBUG Sending `>00`
```

Has anyone ever encountered this issue and/or knows how to fix this?

SasaKaranovic, 2025-09-05:
You have a line that indicates there was a timeout with the serial communication
`Aug 29 2025 19:00:41.050 pid:7 serial_driver.py         145 ERROR Timeout occured (1756494041.0506754 > 1756494040.0444684)`

But you are right, the software should more gracefully handle this edge case where board does not respond and a timeout occurs.

AlphaSoftwareInc, 2025-09-05:
Update: I flashed the firmware with the one from GitHub but still timeouts...

How could I debug this any further? Also, is it know to be incompatible with Raspberry Pis / ARM ?

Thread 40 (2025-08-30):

Does this controller have short-circuit protection?

astrolemonade, 2025-08-30:
Hey!
I recently watched a video about some of the older noctua fan controllers showcasing the short circuit protection in case of faulty fans.
https://youtu.be/YzRLOOlhMsQ
I am curious about how this fan controller behaves in such scenarios.

Also, how does buying from your website works? Do you do batches? If I miss current batch I'll have to wait for the next or I can pre-order without worrying whenever I want? Where are you shipping the products from?
Thank you!

SasaKaranovic, 2025-09-05:
Yes, each fan has a dedicated resettable fuse.
Obviously the best advice would be not to use sketchy/cheap fans. :)

The web shop works and usually all products are kept always in stock.
Obviously sometimes product can temporarily be out of stock due to increased demand but should get back in stock shortly and during this time the web-shop shows "pre-order" sign, but units are already being manufactured regardless. It just means that if you place an order during "pre-order", your board will be shipped as soon as new boards are available (usually 2-3 weeks) instead of the usual ~48hrs.

The "biggest" difference is the USB-C connector and a couple of changes that the PCB shop requests. Otherwise the board is identical, so it's really a negligible change.

I don't want to go on a rant here, so the short answer is; I am still working on a way to better release open source designs...
So hopefully soon.

Closed 2025-09-25.

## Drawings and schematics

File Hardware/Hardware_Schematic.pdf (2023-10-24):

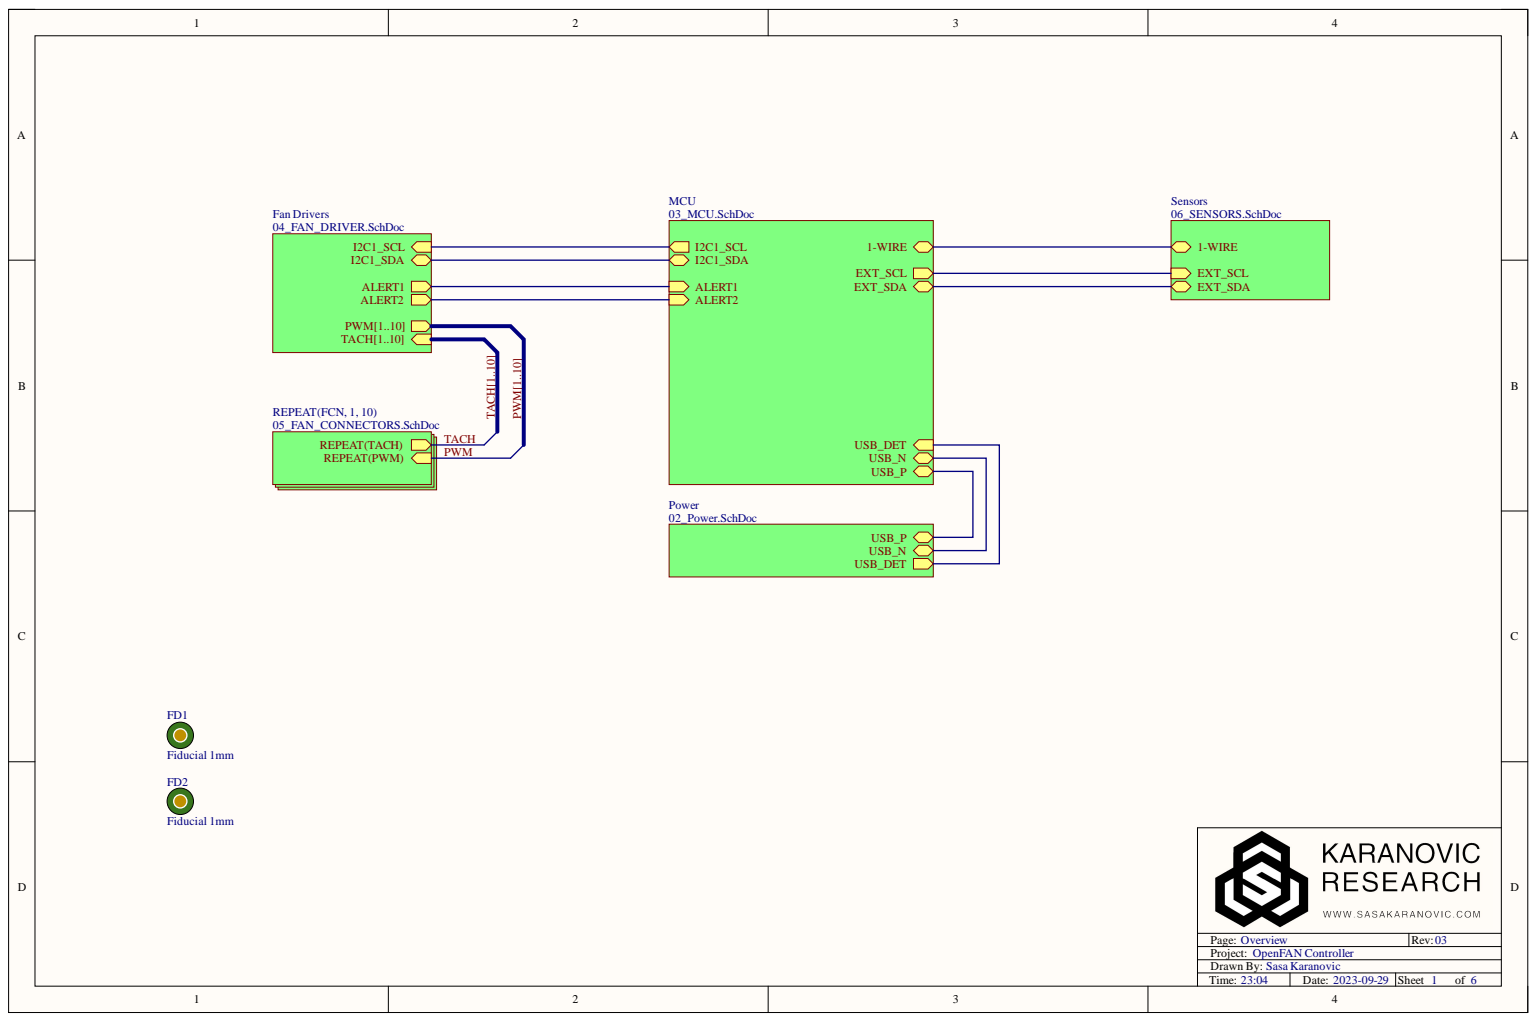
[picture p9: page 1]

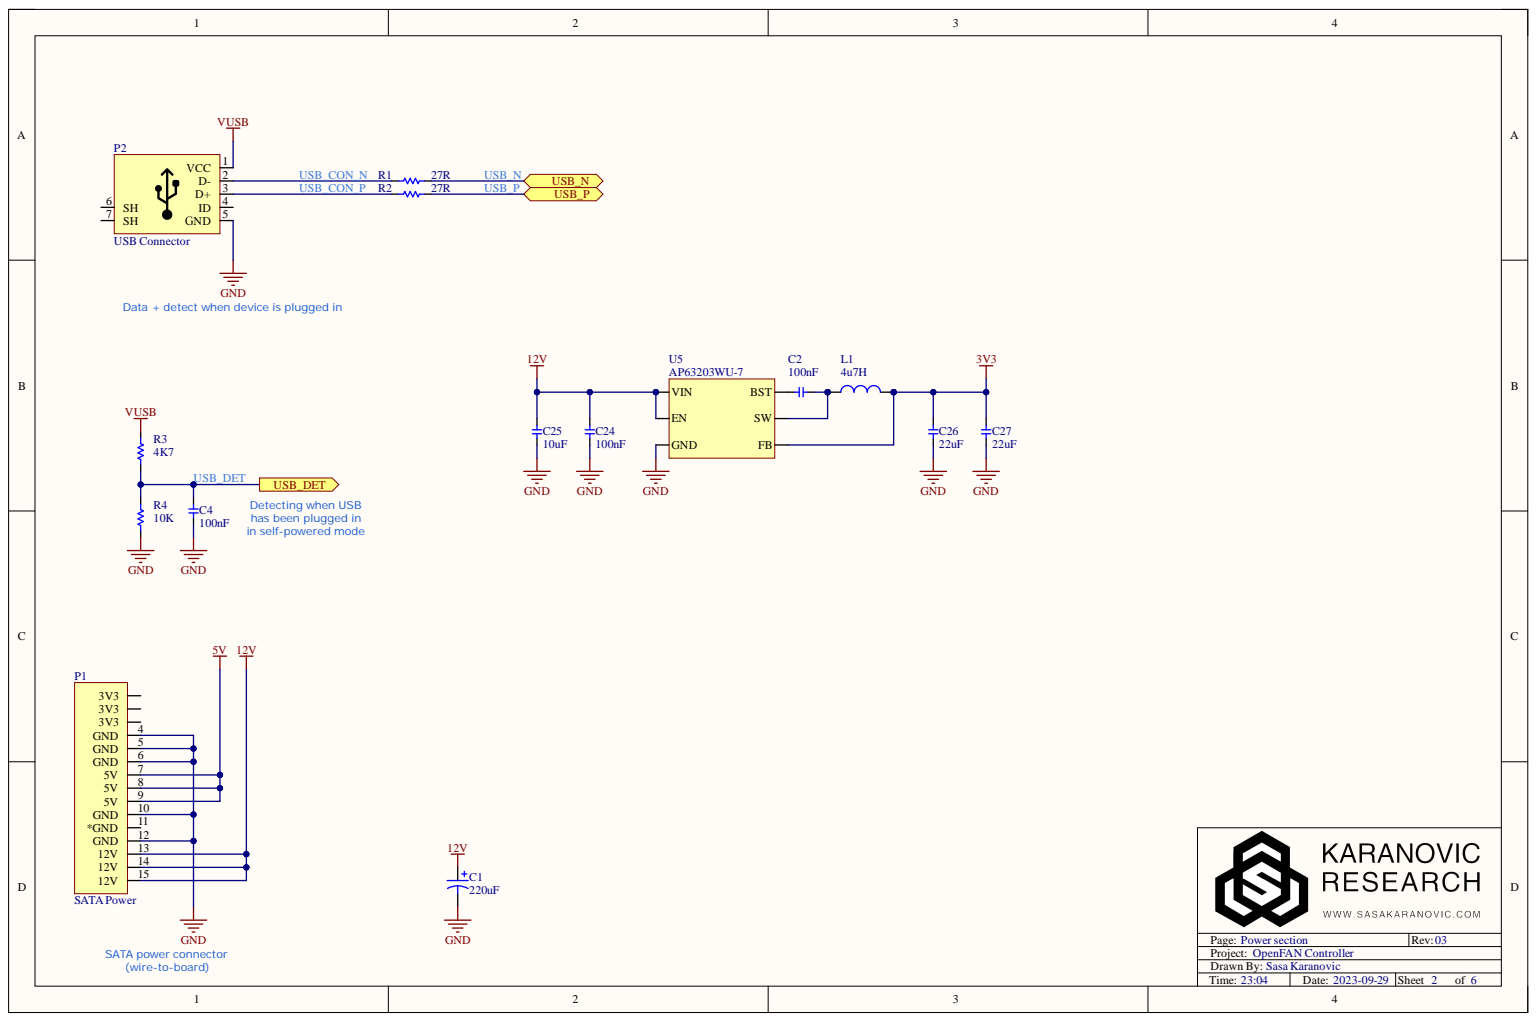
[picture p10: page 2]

Data + detect when device is plugged in

Detecting when USB
has been plugged in
in self-powered mode

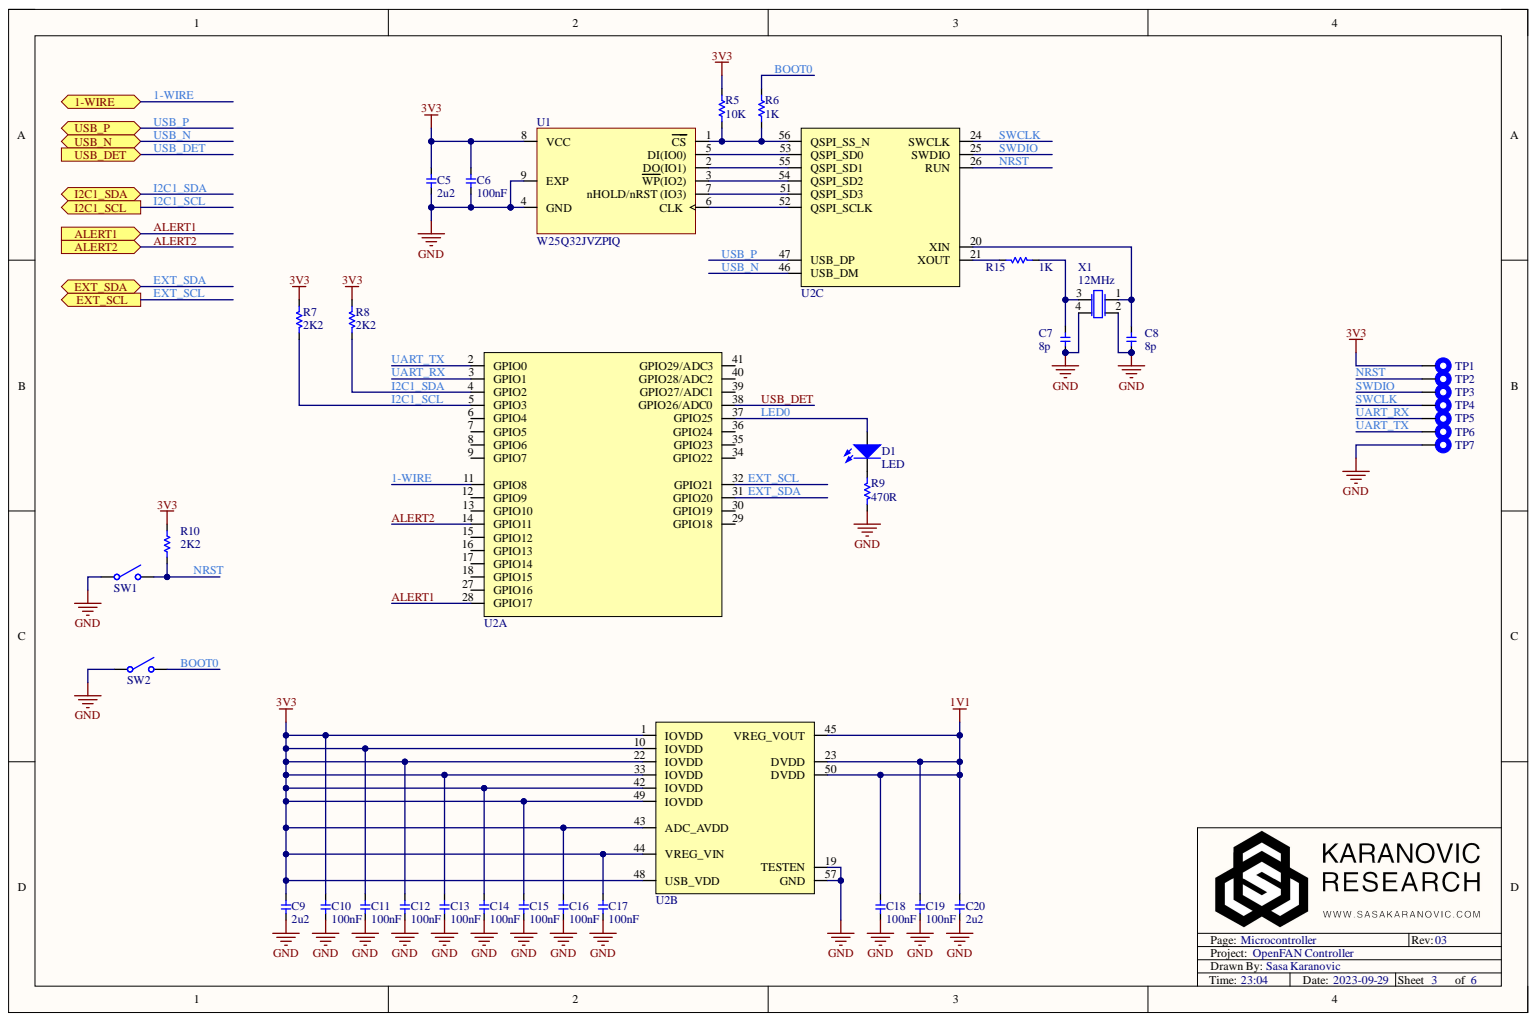
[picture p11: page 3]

IOVDD 42
IOVDD 49

ADC_AVDD 43

VREG_VIN 44

USB_VDD 48

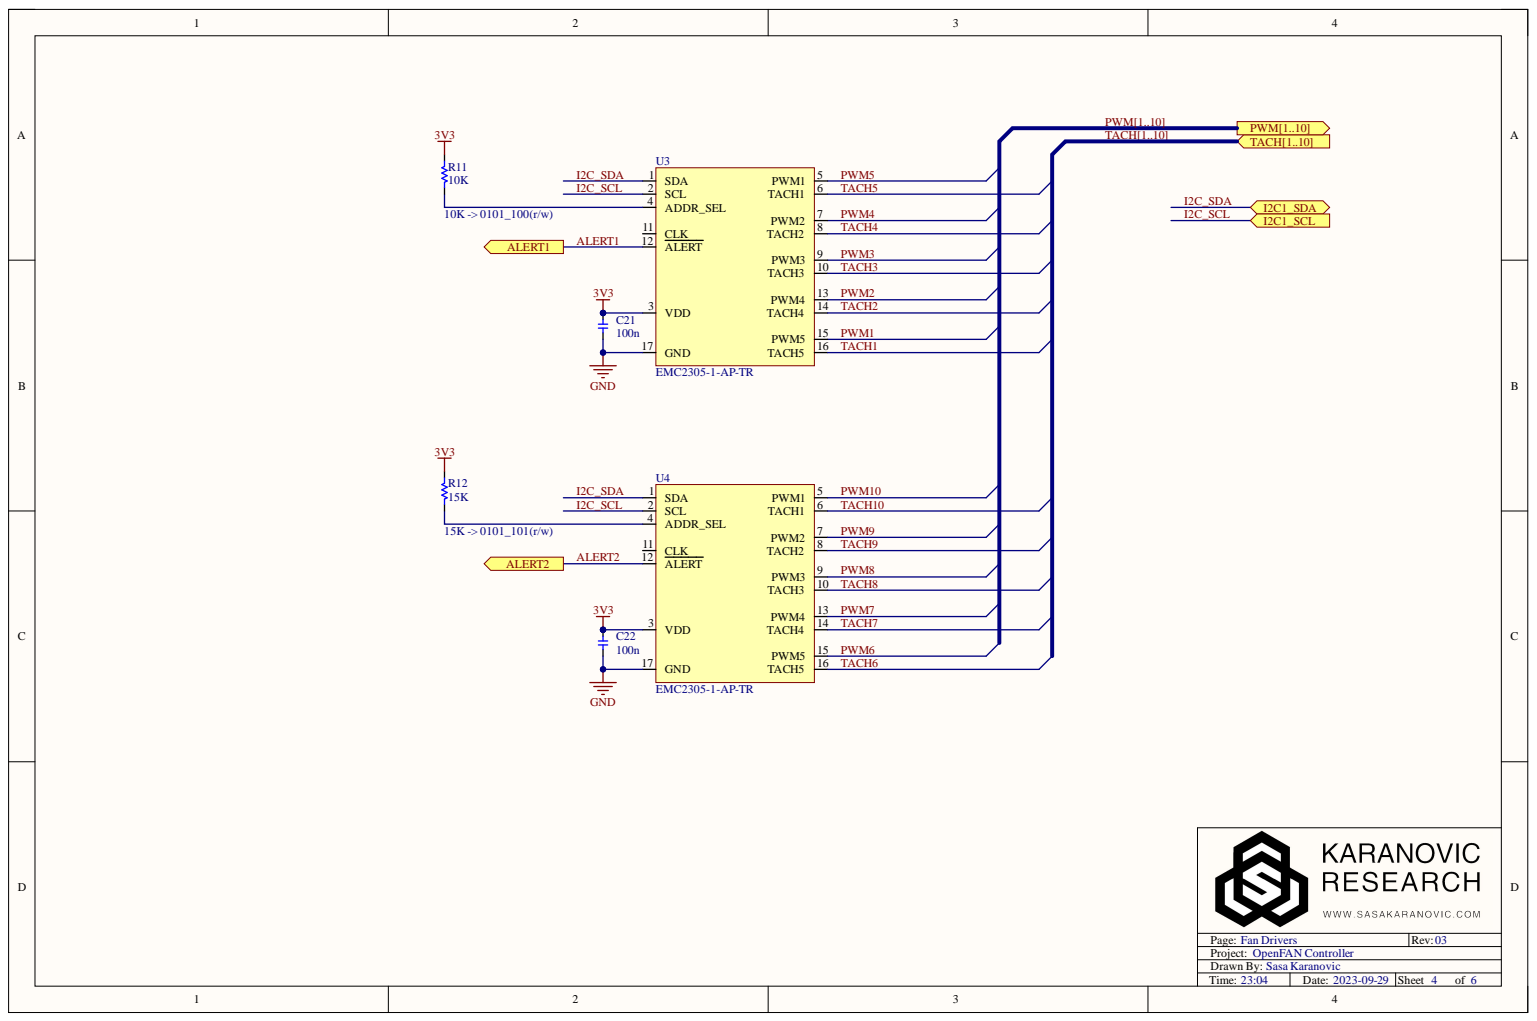
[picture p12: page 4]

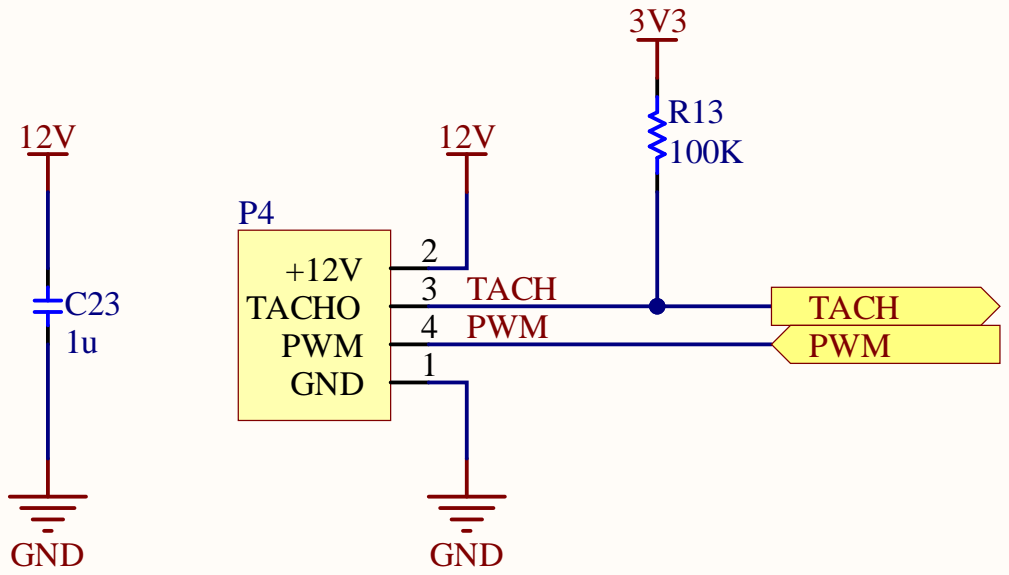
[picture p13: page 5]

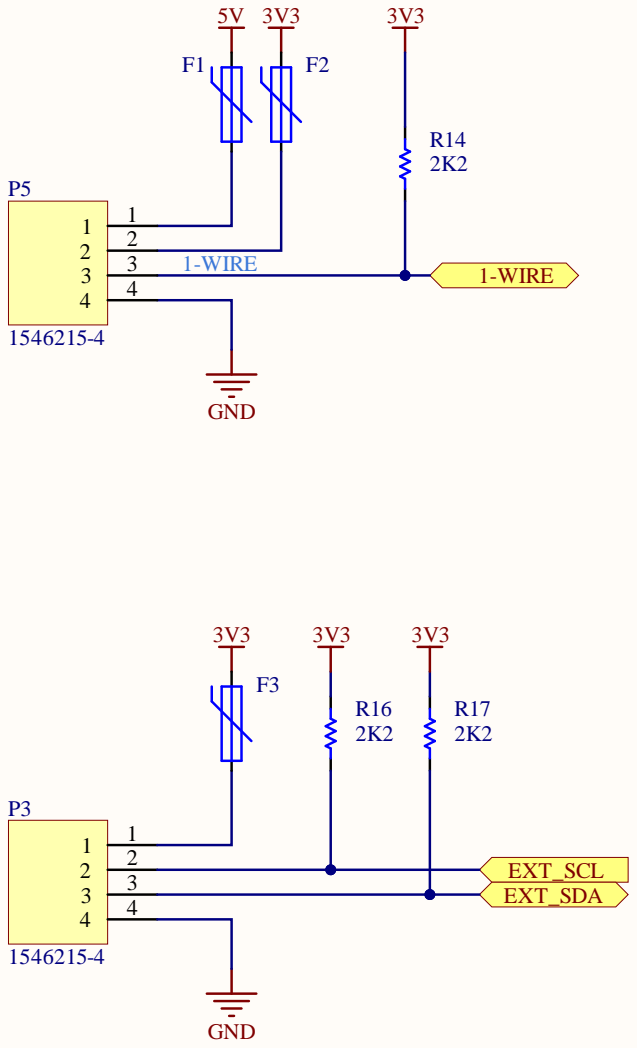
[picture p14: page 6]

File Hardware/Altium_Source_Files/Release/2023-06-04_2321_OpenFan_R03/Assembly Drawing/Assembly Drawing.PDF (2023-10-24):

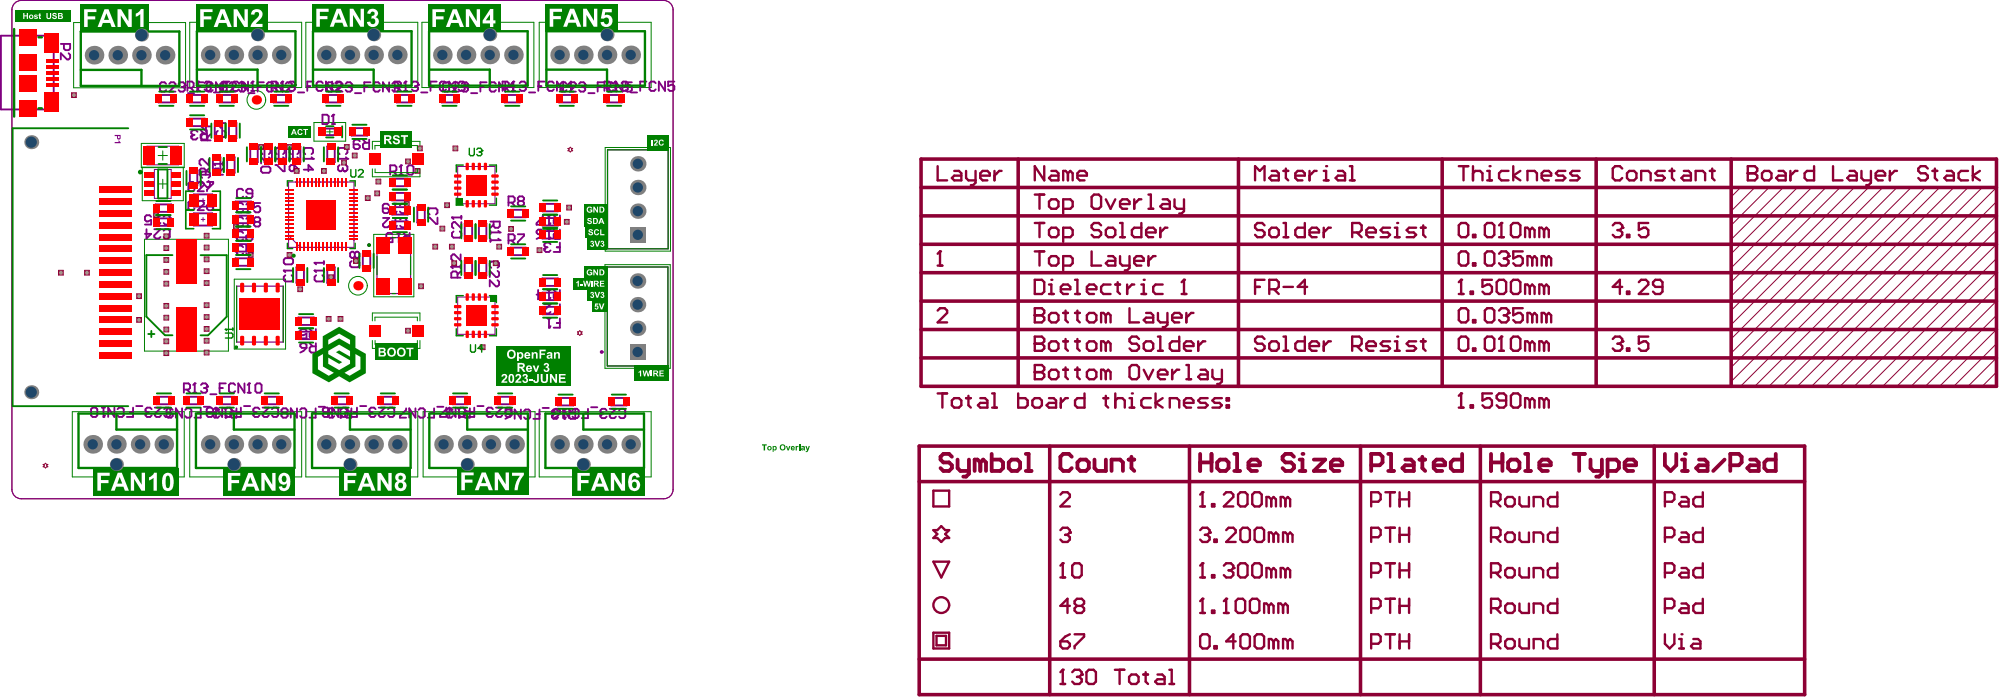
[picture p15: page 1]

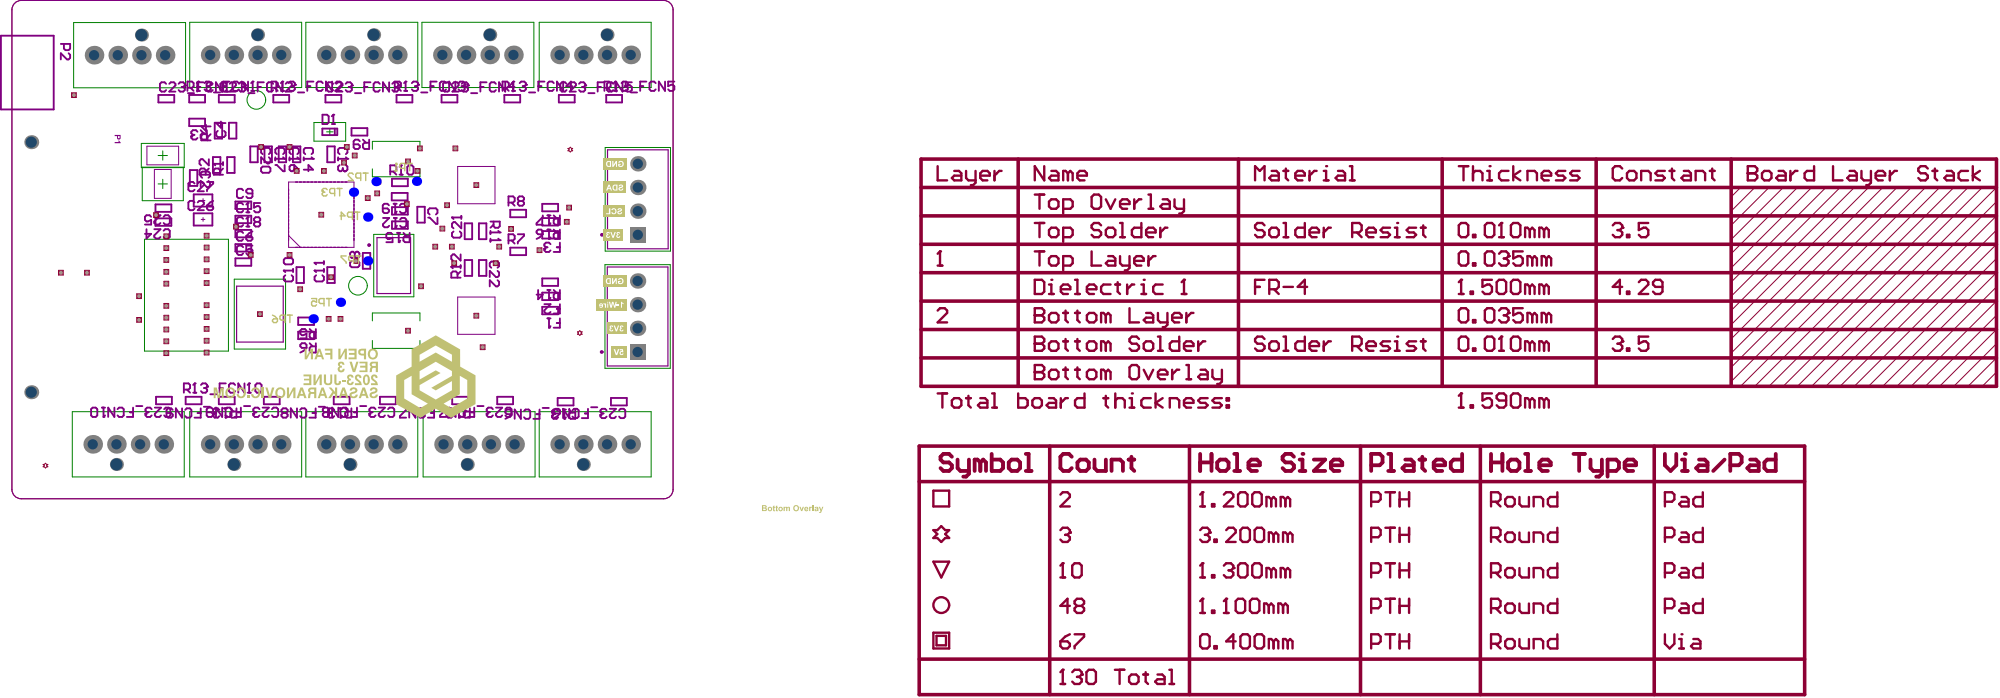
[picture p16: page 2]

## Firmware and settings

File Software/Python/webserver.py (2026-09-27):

import sys
import os
import signal
import argparse
import time
import datetime
import re
from mimetypes import guess_type
from tornado.web import Application
from tornado.web import RequestHandler
from tornado.web import StaticFileHandler
from tornado.web import Finish
from tornado.web import HTTPError
from tornado.ioloop import IOLoop
from FanCommander import FanCommander
from base_logger import logger, set_logger_level
from config import ConfigReader
from board import OpenFAN_Board
from version import get_git_long_hash, get_git_short_hash, get_git_commit_date

BASEDIR_NAME = os.path.dirname(__file__)
BASEDIR_PATH = os.path.abspath(BASEDIR_NAME)
WEBPAGE_ROOT = os.path.join(BASEDIR_PATH, 'webpage')


class BaseHandler(RequestHandler):
    def initialize(self, handler, config, board):
        self.handler = handler
        self.config = config
        self.board = board
        self.limit_fan_index_min = 0
        self.limit_fan_index_max = max(self.board.get_fan_count()-1, 0)
        self.limit_temp_index_min = 0
        self.limit_temp_index_max = max(self.board.get_sensor_count()-1, 0)

    def get_int_argument(self, name, default=0):
        try:
            return int(float(self.get_argument(name, default)))
        except (TypeError, ValueError):
            return None

    def send_error_invalid_value(self):
        return self.send_response(status='error', message='`value` must be a number!', data=None)

    def send_response(self, status, message='', data=None):
        self.write({'status': status, 'message': message, 'data': data})
        return self.finish()

    def set_default_headers(self):
        self.set_header("Access-Control-Allow-Origin", "*")
        self.set_header('Access-Control-Allow-Methods', 'POST, GET')
        self.set_header('Content-Type', 'application/json')

    def is_valid_fan_index(self, index):
        try:
            if int(index) >=self.limit_fan_index_min and int(index) <= self.limit_fan_index_max:
                return True
            return False
        except ValueError:
            return False

    def is_valid_temperature_index(self, index):
        try:
            if int(index) >=self.limit_temp_index_min and int(index) <= self.limit_temp_index_max:
                return True
            return False
        except ValueError:
            return False

    def supports_fan_profiles(self):
        return self.board.board_has_profiles()

    def supports_rpm_control(self):
        return self.board.fw_support_rpm()

    def supports_temperature_sensors(self):
        return self.board.board_has_sensors()

    def send_error_no_profile_support(self):
        return self.send_response(status='error', message=f'Board `{self.board.get_name()}` does not support fan profiles!')

    def send_error_no_rpm_control(self):
        return self.send_response(status='error', message=f'Board `{self.board.get_name()}` does not yet support RPM control!')

    def send_error_no_temperature_sensor_support(self):
        return self.send_response(status='error', message=f'Board `{self.board.get_name()}` does not support temperature sensors!')

class FanProfile_List(BaseHandler):
    def get(self):
        logger.info("Request:FANPROFILE_LIST")
        if not self.supports_fan_profiles():
            return self.send_error_no_profile_support()

        profiles = self.config.get_all_fan_profiles()
        self.send_response(status='ok', message=f'There are {len(profiles)} FAN profiles available.', data=profiles)

class FanProfile_Add(BaseHandler):
    def post(self):
        logger.info("Request:FANPROFILE_ADD")
        if not self.supports_fan_profiles():
            return self.send_error_no_profile_support()

        try:
            profile_name = self.get_argument('name', None)
            profile_type = self.get_argument('type', None)
            profile_values_str = self.get_argument('values', None)
            error = False
            message = ""

            if profile_name is None:
                error = True
                message = 'Fan profile name can not be empty!'
            if profile_type is None:
                error = True
                message='Fan profile type can not be empty!'
            if profile_values_str is None:
                error = True
                message='Fan profile values can not be empty!'
            if profile_type.lower() != 'pwm' and profile_type.lower() != 'rpm':
                error = True
                message='Fan profile type can be either "pwm" or "rpm".'
        except Exception as e:
            logger.error(e)
            error = True

        if error:
            return self.send_response(status='error', message=message, data=None)

        fan_profile = profile_values_str.split(';')
        try:
            fan_profile = [int(i) for i in fan_profile]
        except Exception as e:
            logger.error(f'FanProfile_Add error: {e}')
            return self.send_response(status='error', message='Fan profile can only contain integer values!', data=None)

        if len(fan_profile) != 10:
            return self.send_response(status='error', message=f'Fan profile expects exactly 10 values! ({len(fan_profile)} given)', data=None)

        if self.config.update_fan_profile(profile_name, profile_type, fan_profile):
            return self.send_response(status='ok', message='Profile added', data=None)
        return self.send_response(status='error', message='Failed to add profile!', data=None)

class FanProfile_Remove(BaseHandler):
    def get(self):
        logger.info("Request:FANPROFILE_REMOVE")
        if not self.supports_fan_profiles():
            return self.send_error_no_profile_support()

        name = self.get_argument('name', None)
        if name is None:
            return self.send_response(status='error', message='Name can not be empty!', data=None)

        res = self.config.remove_fan_profile(name)
        if res is True:
            return self.send_response(status='ok', message='Profile removed', data=None)
        return self.send_response(status='ok', message='Profile does not exist', data=None)

class FanProfile_Set(BaseHandler):
    def get(self):
        logger.info("Request:FANPROFILE_SET")
        if not self.supports_fan_profiles():
            return self.send_error_no_profile_support()

        name = self.get_argument('name', None)
        if name is None:
            return self.send_response(status='error', message='Name can not be empty!', data=None)

        profile = self.config.get_fan_profile(name)
        if not profile:
            return self.send_response(status='error', message='Profile does not exist! (Names are case-sensitive!)', data=None)

        profile_type = profile['type'].upper()
        if profile_type not in ["PWM", "RPM"]:
            return self.send_response(
                                      status='error',
                                      message=f'Malformed profile type! (expected "pwm" or "rpm". "{profile_type}" received.)',
                                      data=None)

        profile_values = profile['values']

        msg = ""
        for index, pwm in enumerate(profile_values):
            logger.debug(f"Setting fan {index} to {pwm} {profile_type}")
            msg = msg + f" Fan{index+1}={pwm} {profile_type}"

            if profile_type == 'PWM':
                self.handler.set_fan_pwm(index, pwm)
            else:
                self.handler.set_fan_rpm(index, pwm)

        return self.send_response(status='ok', message=f'Profile `{name}` activated.{msg}.', data=None)

class TemperatureSensor_Handler(BaseHandler):
    def get(self, sensor_index=-1):
        logger.info("Request:TEMPERATURE")
        if not self.supports_temperature_sensors():
            return self.send_error_no_temperature_sensor_support()

        if not self.is_valid_temperature_index(sensor_index):
            return self.send_response(status='error', message=f'Invalid temperature index ({self.limit_temp_index_min}<=`{sensor_index}`<={self.limit_temp_index_max})', data=None)

        temperature = self.handler.get_temperature(int(sensor_index))
        return self.send_response(status='ok', message='', data=temperature)

class TemperatureSensorAll_Handler(BaseHandler):
    def get(self):
        logger.debug("Request:TEMPERATURE_ALL")
        if not self.supports_temperature_sensors():
            return self.send_error_no_temperature_sensor_support()

        temperature = self.handler.get_temperature_all()
        return self.send_response(status='ok', message='', data=temperature)

class FanStatus_Handler(BaseHandler):
    def get(self):
        logger.debug("Request:STATUS")

        rpm = self.handler.get_all_fan_rpm()
        return self.send_response(status='ok', message='', data=rpm)

class FanSetALLPWM(BaseHandler):
    def get(self):
        value = self.get_int_argument('value', 0)
        if value is None:
            return self.send_error_invalid_value()
        if value > 100:
            value = 100
        elif value < 0:
            value = 0

        logger.info(f"Request:SET - FAN: ALL To:{value}%")
        self.handler.set_all_fan_pwm(value)
        return self.send_response(status='ok', message=f'Update queued. Setting ALL fans to PWM:{value}%', data=None)

class FanSetPWM_Handler(BaseHandler):
    def get(self, fan_index=-1):
        if not self.is_valid_fan_index(fan_index):
            return self.send_response(status='error', message=f'Invalid fan index ({self.limit_fan_index_min}<=`{fan_index}`<={self.limit_fan_index_max})', data=None)

        value = self.get_int_argument('value', 0)
        if value is None:
            return self.send_error_invalid_value()
        if value > 100:
            value = 100
        elif value < 0:
            value = 0

        fan_index = int(fan_index)
        logger.info(f"Request:SET - FAN:{fan_index} To:{value}% ({value})")
        self.handler.set_fan_pwm(fan_index, value)
        return self.send_response(status='ok', message=f'Update queued. Setting fan #{fan_index} to PWM:{value}%', data=None)

class FanSetRPM_Handler(BaseHandler):
    def get(self, fan_index=-1):
        if not self.supports_rpm_control():
            return self.send_error_no_rpm_control()

        if not self.is_valid_fan_index(fan_index):
            return self.send_response(status='error', message=f'Invalid fan index ({self.limit_fan_index_min}<=`{fan_index}`<={self.limit_fan_index_max})', data=None)

        value = self.get_int_argument('value', 0)
        if value is None:
            return self.send_error_invalid_value()
        if value > 16000:
            value = 16000
        elif value < 480:
            value = 0

        # Fan index is specified
        fan_index = int(fan_index)
        logger.info(f"Request:SET RPM - FAN:{fan_index} To:{value} RPM")
        self.handler.set_fan_rpm(fan_index, value)
        return self.send_response(status='ok', message=f'Update queued. Fan:{fan_index} RPM:{value}', data=None)

class FanAliasAll_Handler(BaseHandler):
    def get(self):
        logger.info("Request:GET ALL FAN Aliases")
        aliases = self.config.get_fan_alias(-1)
        fan_data = {}
        for fan_index, alias in aliases.items():
            fan_data[fan_index] = alias

        return self.send_response(status='ok', message='', data=fan_data)

class FanAliasGet_Handler(BaseHandler):
    def get(self, fan_index=-1):
        if not self.is_valid_fan_index(fan_index):
            return self.send_response(status='error', message=f'Invalid fan index ({self.limit_fan_index_min}<=`{fan_index}`<={self.limit_fan_index_max})', data=None)

        # Fan index is specified
        fan_index = int(fan_index)
        logger.info(f"Request:GET FAN Alias - FAN:{fan_index}")
        fan_data = { 'fan_id': fan_index, 'alias': self.config.get_fan_alias(fan_index)}
        return self.send_response(status='ok', message='', data=fan_data)

class FanAliasSet_Handler(BaseHandler):
    def get(self, fan_index=-1):
        if not self.is_valid_fan_index(fan_index):
            return self.send_response(status='error', message=f'Invalid fan index ({self.limit_fan_index_min}<=`{fan_index}`<={self.limit_fan_index_max})', data=None)

        value = self.get_argument('value', None)
        if value is None:
            return self.send_response(status='error', message='Fan alias can not be none!', data=None)
        if re.search(r"^[a-z0-9\-_\.# ]*?$", value, re.MULTILINE | re.IGNORECASE) is None:
            return self.send_response(status='error', message='Fan alias can only contain `A-Z`, `0-9`, `-`, `_`, `#` and `<space>` characters!', data=None)

        # Fan index is specified
        fan_index = int(fan_index)
        logger.info(f"Request:SET FAN #{fan_index} alias to: `{value}`")
        if self.config.set_fan_alias(fan_index, value):
            return self.send_response(status='ok', message=f'Fan #{fan_index} alias set to:`{value}`', data=None)
        return self.send_response(status='error', message=f'Failed to set fan alias. (`{fan_index}:{value}`)', data=None)

class Info_Handler(BaseHandler):
    def get(self):
        data = {    'hardware': self.handler.get_hw_info(),
                    'firmware': self.handler.get_fw_info(),
                    'software': f"Version: v{get_git_commit_date()} Build: {get_git_short_hash()}",
                    'capabilities': self.board.get_board_capabilities()
        }

        return self.send_response(status='ok', message='System information', data=data)

# -- Default 404 --
class Default_404_Handler(RequestHandler):
    # Override prepare() instead of get() to cover all possible HTTP methods.
    def prepare(self):
        self.set_status(404)
        self.write({'status': 'fail', 'message': 'Unsupported method'})
        raise Finish()

class FileHandler(RequestHandler):
    def get(self, path=None):
        logger.debug(f"Requesting: {path}")
        if path:
            file_location = os.path.join(WEBPAGE_ROOT, path)
        else:
            file_location = os.path.join(WEBPAGE_ROOT, 'index.html')

        if not os.path.isfile(file_location):
            logger.error(f"Requested file can not be found: {path}")
            raise HTTPError(status_code=404)
        content_type, _ = guess_type(file_location)
        self.add_header('Content-Type', content_type)
        with open(file_location, encoding="utf8") as source_file:
            self.write(source_file.read())

class HTMLTemplateHandler(BaseHandler):
    def get(self, re_match=None):

        logger.debug(f"HTMLTemplateHandler: {re_match}")
        board = self.board.get_board_capabilities()
        data = {}

        data['year'] = datetime.datetime.now().year
        data['commit_short_hash'] = get_git_short_hash()
        data['commit_long_hash'] = get_git_long_hash()
        data['commit_time'] = get_git_commit_date()

        self.set_header('Content-Type', 'text/html')
        if re_match:
            self.render(f'{re_match}.html', board=board, data=data)
        else:
            self.render('index.html', board=board, data=data)


class JSTemplateHandler(BaseHandler):
    def get(self, re_match=None):

        logger.debug(f"JSTemplateHandler: {re_match}")
        board = self.board.get_board_capabilities()
        data = {}

        data['year'] = datetime.datetime.now().year
        data['commit_short_hash'] = get_git_short_hash()
        data['commit_long_hash'] = get_git_long_hash()
        data['commit_time'] = get_git_commit_date()

        self.set_header('Content-Type', 'text/javascript')
        if re_match:
            self.render(f'assets/js/openfan_{re_match}.js', board=board, data=data)
        else:
            self.write("")



def build_handlers(fan_commander, config, board):
    """Return the Tornado URL routing table.

    Kept separate from `FAN_API_Service` so the API can be built (e.g. in unit tests)
    with any object that implements the `FanCommander` interface, without real hardware.
    """
    ctx = {"handler": fan_commander, "config": config, "board": board}
    return [
        (r"/api/v0/profiles/list", FanProfile_List, ctx),
        (r"/api/v0/profiles/add", FanProfile_Add, ctx),
        (r"/api/v0/profiles/remove", FanProfile_Remove, ctx),
        (r"/api/v0/profiles/set", FanProfile_Set, ctx),
        (r"/api/v0/fan/status", FanStatus_Handler, ctx),
        (r"/api/v0/sensor/temperature/([0-9])/get", TemperatureSensor_Handler, ctx),
        (r"/api/v0/sensor/temperature/all/get", TemperatureSensorAll_Handler, ctx),
        (r"/api/v0/fan/all/set", FanSetALLPWM, ctx),
        # !!NOTE!! `/api/v0/fan/([0-9])/set` is now deprecated. Please use `/api/v0/fan/([0-9])/pwm`
        (r"/api/v0/fan/([0-9])/set", FanSetPWM_Handler, ctx),
        (r"/api/v0/fan/([0-9])/pwm", FanSetPWM_Handler, ctx),
        (r"/api/v0/fan/([0-9])/rpm", FanSetRPM_Handler, ctx),
        (r"/api/v0/alias/all/get", FanAliasAll_Handler, ctx),
        (r"/api/v0/alias/([0-9])/get", FanAliasGet_Handler, ctx),
        (r"/api/v0/alias/([0-9])/set", FanAliasSet_Handler, ctx),
        (r"/api/v0/info", Info_Handler, ctx),
        (r"/", HTMLTemplateHandler, ctx),
        (r"/(.*)\.html", HTMLTemplateHandler, ctx),
        (r"/assets/js/openfan_(.*)\.js", JSTemplateHandler, ctx),
        (r"/", FileHandler),
        (r'/(.*)', StaticFileHandler, {'path': WEBPAGE_ROOT}),
    ]


DEFAULT_SERVER_SETTINGS = {
    "debug": True,
    # "autoreload": False,
    "autoreload": True,
    "default_handler_class": Default_404_Handler,
    "template_path": "webpage",
    # "template_whitespace": "single"
    "template_whitespace": "all"
}


def make_app(fan_commander, config, board, **settings_overrides):
    """Create the Tornado `Application` without opening a serial port.

    `settings_overrides` are merged over `DEFAULT_SERVER_SETTINGS`
    (tests use this to disable `debug`/`autoreload`).
    """
    settings = dict(DEFAULT_SERVER_SETTINGS)
    settings.update(settings_overrides)
    return Application(build_handlers(fan_commander, config, board), **settings)


class FAN_API_Service(Application):
    def __init__(self):

        # OpenFAN config file (ie `config.yaml`) path can be set through `OPENFANCONFIG` environment variable
        # or if it's not set, the default `config.yaml` from this directory will be used.
        config_file = os.getenv('OPENFANCONFIG', default='config.yaml')
        self.config = ConfigReader(config_file)

        # API service will look for OpenFAN serial port in the following order
        # 1. Check if `hardware->port` entry is specified in `config.yaml`
        # 2. Check if `OPENFANCOMPORT` is specified in OS environment variable
        # 3. Try to find OpenFAN controller by searching for USB VID and PID

        hardware_config = self.config.get_hardware_config()
        cfg_port = hardware_config.get('port', None)
        env_port = os.getenv('OPENFANCOMPORT', default=None)

        if cfg_port:
            self.serialPort = cfg_port
            logger.info(f"Using COM port `{self.serialPort}` (specified in `config.yaml` file).")
        elif env_port is not None:
            self.serialPort = env_port
            logger.info(f"Using COM port `{self.serialPort}` (specified in `OPENFANCOMPORT` env variable).")
        else:
            self.serialPort = FanCommander.find_fan_controller()
            if self.serialPort is None:
                logger.error("Could not find Fan controller. Please make sure it's plugged in and (if necessary) drivers are installed.")
                raise Exception("Could not find Fan controller. Please make sure it's plugged in and (if necessary) drivers are installed.")

            logger.info(f"Using COM port `{self.serialPort}` (Found through USB VID:PID).")

        logger.info("Fan Controller port: {}".format(self.serialPort))
        self.fan_commander = FanCommander(self.serialPort)
        self.board = OpenFAN_Board(self.fan_commander.get_hw_info(), self.fan_commander.get_fw_info())

        self.handlers = build_handlers(self.fan_commander, self.config, self.board)
        self.server_settings = dict(DEFAULT_SERVER_SETTINGS)

    def run_forever(self):
        logger.info("Karanovic Research OpenFan - Starting API server")
        app = Application(self.handlers, **self.server_settings)

        server_config = self.config.get_server_config()
        port = server_config.get('port', 3000)
        logger.info(f"Listening on port {port}")
        app.listen(port)

        IOLoop.instance().start()


def signal_handler(signal, frame):
    IOLoop.current().add_callback_from_signal(shutdown)
    print('\r\nYou pressed Ctrl+C!')
    sys.exit(0)

def shutdown():
    logger.info('Stopping API server')
    logger.info('Will shutdown in 3 seconds ...')
    io_loop = IOLoop.instance()
    deadline = time.time() + 3

    def stop_loop():
        now = time.time()
        if now < deadline and (io_loop._callbacks or io_loop._timeouts):
            io_loop.add_timeout(now + 1, stop_loop)
        else:
            io_loop.stop()
            logger.info('Shutdown')
    stop_loop()


def main(cmd_args):
    signal.signal(signal.SIGTERM, signal_handler)
    signal.signal(signal.SIGINT, signal_handler)
    set_logger_level(cmd_args.logging)
    try:
        FAN_API_Service().run_forever()
    except Exception:
        logger.exception("OpenFan API service crashed during setup.")
    os._exit(0)

if __name__ == '__main__':
    parser = argparse.ArgumentParser(description='Karanovic Research - Fan Controller API service')
    parser.add_argument('-l', '--logging', type=str, default='info')
    args = parser.parse_args()
    main(args)

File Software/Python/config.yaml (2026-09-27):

server:
  hostname: localhost
  port: 3000
hardware:
  port:
  communication_timeout: 1
fan_profiles:
  50% PWM:
    type: pwm
    values:
    - 50
    - 50
    - 50
    - 50
    - 50
    - 50
    - 50
    - 50
    - 50
    - 50
    name: 50% PWM
  100% PWM:
    type: pwm
    values:
    - 100
    - 100
    - 100
    - 100
    - 100
    - 100
    - 100
    - 100
    - 100
    - 100
    name: 100% PWM
  1000 RPM:
    type: rpm
    values:
    - 1000
    - 1000
    - 1000
    - 1000
    - 1000
    - 1000
    - 1000
    - 1000
    - 1000
    - 1000
    name: 1000 RPM
  Test:
    type: RPM
    values:
    - 1000
    - 1000
    - 1000
    - 1000
    - 1000
    - 1000
    - 1000
    - 1000
    - 1000
    - 1000
    name: Test
  Test2:
    type: PWM
    values:
    - 50
    - 50
    - 50
    - 50
    - 50
    - 50
    - 50
    - 50
    - 50
    - 50
fan_aliases:
  0: 'Fan #1'
  1: 'Fan #2'
  2: 'Fan #3'
  3: 'Fan #4'
  4: 'Fan #5'
  5: 'Fan #6'
  6: 'Fan #7'
  7: 'Fan #8'
  8: 'Fan #9'
  9: 'Fan #10'

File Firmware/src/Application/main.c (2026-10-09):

#include <tusb.h>
#include <pico/multicore.h>
#include <hardware/clocks.h>
#include "pico/bootrom.h"
#include "board.h"
#include "fan_control.h"
#include "host_communication.h"
#include "usb_cdc.h"

#define MIN_LOG_LEVEL_DEBUG
#define LOGGER_TAG "MAIN"
#include "logger.h"


bool led_state = false;

bool systick_callback(repeating_timer_t *rt);

bool reserved_addr(uint8_t addr) {
    return (addr & 0x78) == 0 || (addr & 0x78) == 0x78;
}

int main(void)
{
    set_sys_clock_khz(250000, false);
    stdio_init_all();

    gpio_init(LED_PIN);
    gpio_set_dir(LED_PIN, GPIO_OUT);

    i2c_init(PICO_I2C_INSTANCE, 400 * 1000);
    gpio_set_function(PICO_I2C_SDA_PIN, GPIO_FUNC_I2C);
    gpio_set_function(PICO_I2C_SCL_PIN, GPIO_FUNC_I2C);

    fan_control_init();
    host_comm_init();

#ifndef CFG_NOLED_BLINK
    // Setup systick timer
    repeating_timer_t timer;
    // negative timeout means exact delay (rather than delay between callbacks)
    if (!add_repeating_timer_us(-500000, systick_callback, NULL, &timer)) {
        gpio_put(LED_PIN, 1);
        return 1;
    }
#endif

    Logger_INFO("Up and running");

    usbd_serial_init();
    tusb_init();
    while (1) {
        usb_cdc_tick();
        fan_periodic_tick();
        host_comm_tick();
    }

    return 0;
}

#ifndef CFG_NOLED_BLINK
bool systick_callback(repeating_timer_t *rt)
{
    gpio_put(LED_PIN, led_state);
    led_state = !led_state;
    return true; // keep repeating
}
#endif

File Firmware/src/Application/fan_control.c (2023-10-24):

#include "board.h"
#include "emc230x.h"
#include "fan_control.h"

#define MIN_LOG_LEVEL_INFO
#define LOGGER_TAG "FC"
#include "logger.h"

#define FAN_TICK_PERIOD         1000

uint32_t nFanTick = 0;
uint16_t fan_rpm[NUM_TOTAL_FAN] = {0};

// --- NOTE ---
// There are dedicated commands for operations that target all fans
// FANS are split into multiple banks.
// Fan index starts at 0 and ends at NUM_TOTAL_FAN-1.
//  -> Software will deal with converting zero indexed values to one indexed values
//  -> Firmware will deal with mapping logical channels to physical location


// End user and software will use FAN numbers as they appear on the PCB silkscreen (ie. 1-10).
// We call this logical channel number. The firmware will then take that logical number and convert
// it to physical mapping. Reason for this is because we can have multiple controllers that have
// same channels and/or that logical number (ie. FAN3) does not have to be physicall FAN3.
// Hopefully this is clear, but here is also the actual mapping to make things clearer

// Logical Fan Index (zero-indexed)                       1  2  3  4  5  6  7  8  9  10
static const uint8_t fan_controller_map[NUM_TOTAL_FAN] = {0, 0, 0, 0, 0, 1, 1, 1, 1, 1};    // Map fan to controller
static const uint8_t fan_channel_map[NUM_TOTAL_FAN]    = {4, 3, 2, 1, 0, 4, 3, 2, 1, 0};    // Map fan to channel
// Let's take fan index 3 which is this one                     ^
//                                                              |--- > If we read the map, it tells us that our logical
//                                                                     fan #3 is connected to the controller #0
//                                                                     and it's connected to it's channel #2.
//                                                                     In order to controll this fan we need to talk to
//                                                                     controller #0 and set/get channel #2 values.

static void switch_fan_controller_to(uint8_t controller);
static uint8_t map_channel_to_controller(uint8_t channel);



void fan_control_init(void)
{
    Logger_INFO("---Fan Controller---");
    Logger_INFO("Fan Controllers: %d", NUM_CONTROLLERS);
    Logger_INFO("Fans per controller: %d", NUM_FAN_PER_CONTROLLER);
    Logger_INFO("Total fans: %d", NUM_TOTAL_FAN);
    // Initialize each controller
    for (uint8_t i=0; i<NUM_CONTROLLERS; i++)
    {
        switch_fan_controller_to(i);
        emc230x_config_fans();
    }

    // Set all fans to 1k RPM
    for (uint8_t i=0; i<NUM_TOTAL_FAN; i++)
    {
        fan_control_set_fan_rpm(i, 1000);
    }
}

void fan_periodic_tick(void)
{
    if (time_us_32() >= nFanTick)
    {
        // Read RPM of all fans
        for(uint8_t i=0; i<NUM_TOTAL_FAN; i++)
        {
            switch_fan_controller_to(fan_controller_map[i]);
            emc230x_read_fan_rpm(fan_channel_map[i], &fan_rpm[i]);;
        }

        Logger_DEBUG("1:%4d 2:%4d 3:%4d 4:%4d 5:%4d 6:%4d 7:%4d 8:%4d 9:%4d 10:%4d",
                     fan_rpm[0],
                     fan_rpm[1],
                     fan_rpm[2],
                     fan_rpm[3],
                     fan_rpm[4],
                     fan_rpm[5],
                     fan_rpm[6],
                     fan_rpm[7],
                     fan_rpm[8],
                     fan_rpm[9]
                     );

        // uint8_t reg=0;

        // emc230x_read_register(0x25, &reg);
        // Logger_INFO("Fan Stall: 0x%02X", reg);

        // emc230x_read_register(0x26, &reg);
        // Logger_INFO("Fan SPIN: 0x%02X", reg);

        // emc230x_read_register(0x27, &reg);
        // Logger_INFO("Driver Fail: 0x%02X", reg);

        // emc230x_read_register(0x32, &reg);
        // Logger_INFO("Fan 1: 0x%02X", reg);


        nFanTick = time_us_32() + FAN_TICK_PERIOD;
    }
}

void fan_control_read_fan_rpm(uint8_t fan, uint16_t *pRPM)
{
    #if 1
    if(pRPM == NULL)
    {
        Logger_ERROR("%s: Null pointer. Aborting!", __FUNCTION__);
        return;
    }
    if(fan >= NUM_TOTAL_FAN)
    {
        Logger_ERROR("%s: Requested fan index (%d) is out of bounds", __FUNCTION__, fan);
        *pRPM = 0;
        return;
    }

    *pRPM = fan_rpm[fan];

    #else
    fan = map_channel_to_controller(fan);
    emc230x_read_fan_rpm(fan, pRPM);
    Logger_DEBUG("%s: Fan:%d RPM:%d", __FUNCTION__, fan, *pRPM);
    #endif
}

void fan_control_read_all_rpm(uint16_t *pRPM, uint8_t nLen)
{
    if(pRPM == NULL)
    {
        Logger_ERROR("%s: Null pointer! Aborting.", __FUNCTION__);
        return;
    }
    if(nLen > NUM_TOTAL_FAN)
    {
        Logger_ERROR("%s: Requested number of fans (%d) is greater than total number of fans (%d). Clipping.", __FUNCTION__, nLen, NUM_TOTAL_FAN);
        nLen = NUM_TOTAL_FAN;
    }

    for(uint8_t i=0; i<nLen; i++)
    {
        pRPM[i] = fan_rpm[i];
    }
}


void fan_control_set_fan_rpm(uint8_t fan, uint16_t nRPM)
{
    if(fan>=NUM_TOTAL_FAN)
    {
        Logger_ERROR("%s: Requested fan index (%d) is out of bounds", __FUNCTION__, fan);
        return;
    }

    Logger_DEBUG("%s: Fan:%d RPM:%d", __FUNCTION__, fan, nRPM);
    switch_fan_controller_to(fan_controller_map[fan]);
    emc230x_set_target_rpm(fan_channel_map[fan], nRPM);
}

void fan_control_set_fan_pwm(uint8_t fan, uint8_t pwm)
{
    if(pwm>255)
    {
        Logger_ERROR("%s: Requested PWM[%d] > 255. Clipping to 255", __FUNCTION__, pwm);
        pwm = 255;
    }
    if(fan>=NUM_TOTAL_FAN)
    {
        Logger_ERROR("%s: Requested fan index (%d) is out of bounds", __FUNCTION__, fan);
        return;
    }

    Logger_DEBUG("%s: Fan:%d PWM:%d", __FUNCTION__, fan, pwm);
    switch_fan_controller_to(fan_controller_map[fan]);
    emc230x_set_pwm(fan_channel_map[fan], pwm);
}

void fan_control_set_all_pwm(uint8_t pwm)
{
    if(pwm>255)
    {
        Logger_ERROR("%s: Requested PWM[%d] > 255. Clipping to 255", __FUNCTION__, pwm);
        pwm = 255;
    }

    Logger_DEBUG("%s: Setting ALL fans to PWM:%d", __FUNCTION__, pwm);
    // We are setting all fans to same value so channel/controller mapping is irrelevant
    for(uint8_t controller=0; controller<NUM_CONTROLLERS; controller++)
    {
        for(uint8_t fan=0; fan<NUM_FAN_PER_CONTROLLER; fan++)
        {
            switch_fan_controller_to(controller);
            emc230x_set_pwm(fan, pwm);
        }
    }
}

static void switch_fan_controller_to(uint8_t controller)
{
    if(controller==0)
    {
        emc230x_set_address(EMC_CTRL_1_ADDRESS);
    }
    else if(controller==1)
    {
        emc230x_set_address(EMC_CTRL_2_ADDRESS);
    }
    else
    {
        Logger_ERROR("%s: Unknown or unsupported controller!", __FUNCTION__);
    }
}
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

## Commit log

2023-10-24 Initial OpenFan Controller release
    [01_Top.SchDoc, 02_Power.SchDoc, 03_MCU.SchDoc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]
2023-11-04 Adding logger printout to indicate which port cfg was used.
2024-01-28 Updating VID and PID for OpenFAN Pico2040 version.
2024-01-28 Specifying encoding. Updating logger statements. Fixing typo in shutdown handler.
    [webserver.py]
2024-02-07 Adding enclosure files.
    [Enclosure_OpenFAN_Bottom.stl, Enclosure_OpenFAN_Top.stl, Fusion360_OpenFAN_Enclosure.f3z]
2024-02-23 Adding enclosure with better snap features and with out threaded inserts.
    [Enclosure_OpenFAN_Bottom.stl, Enclosure_OpenFAN_Top.stl]
2024-02-23 Adding Fusion360 enclosure design file.
    [Fusion360_OpenFAN_Enclosure.f3z]
2024-05-25 Fixing a typo in radio button logic. (Issue #10)
2024-06-02 Adding `/api/v0/fan/([0-9])/pwm` and deprecating `/api/v0/fan/([0-9])/set`. Still keeping both to preserve backwards compatibility.
2024-06-02 Optimizing imports. Refactoring comments. Refactoring error messaging.
    [serial_driver.py, webserver.py]
2024-06-02 Adding feature to add fan alias.
2024-06-02 Extending enclosure height by 2mm to fit latest batch of boards.
    [Enclosure_OpenFAN_Bottom.stl, Enclosure_OpenFAN_Top.stl, Fusion360_OpenFAN_Enclosure.f3z]
2024-06-20 Explicitly vaiwing pylint error possibly-used-before-assignment
    [serial_driver.py]
2024-07-01 Adding 2023-10-28 release package.
    [2023-10-28_22-03_OpenFAN_PC_PI_PCB.GBL, 2023-10-28_22-03_OpenFAN_PC_PI_PCB.GBO, 2023-10-28_22-03_OpenFAN_PC_PI_PCB.GBP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]
2024-07-01 Updating 100nF PN
    [2023-10-30_10-06_OpenFAN_PC_PI_BOM.xlsx]
2024-07-22 Switchin to using locally hosted font files.
2025-01-03 Adding new enclosure (by Sam Chan).
    [Bottom-PCB-Enclosure_by_Sam_Chan.3mf, Enclosure_OpenFAN_Bottom.stl, Enclosure_OpenFAN_Top.stl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]
2025-03-11 Adding enclosure by Joe Dutson
    [Bottom-PCB-Enclosure_by_Sam_Chan.3mf, Enclosure_OpenFAN_Bottom.stl, Enclosure_OpenFAN_Top.stl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]
2026-01-19 Properly handle i2c transaction.
